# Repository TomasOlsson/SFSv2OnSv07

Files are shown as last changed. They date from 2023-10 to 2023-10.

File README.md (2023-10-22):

# SFSv2OnSv07
How to add BTT SFS V2.0 on Sovol Sv07 and Sv07 Plus

Join our discord server Just another 3D printer community: https://discord.gg/SBAAEH9qnD

# What you need
1. SFS V2.0
2. Printed part of couplerholderV0.3.3mf and SFSV2Holder.3mf
3. Tools

**IF YOU HAVE AN SV07 PLUS, YOU WILL NEED TO EXTEND THE CABLE THAT COMES WITH THE SFS V2.0 OR BUY A LONGER ONE.**

# How to
1. Remove the button plate of the printer.
2. Unconnect the old filament Runout sensor and remove it.
3. Connect the SFS V2.0.

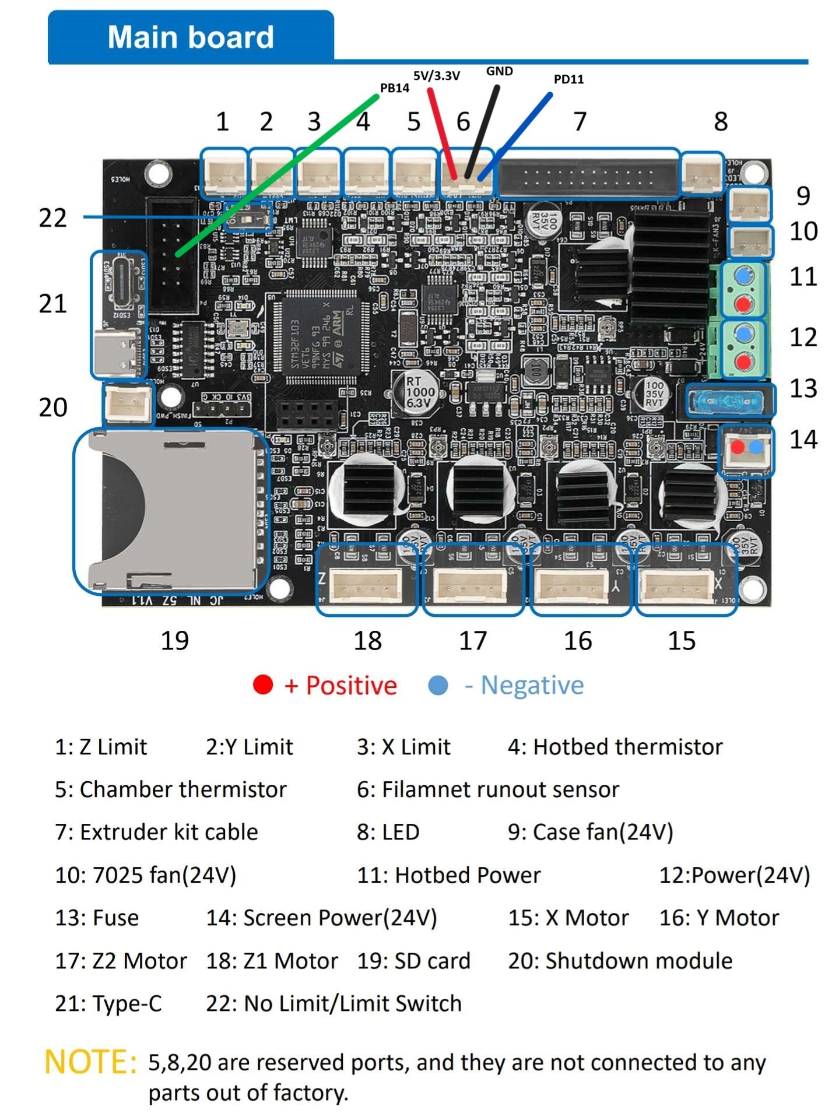
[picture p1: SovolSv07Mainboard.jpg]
Mainboard


4. Run the SFS V2.0 wire where the old runout sensor wire is.
5. Mount the printed parts and the SFS V2.0
6. Add the button plate of the printer.
7. Start printer.
8. Edit printer.cfg

   Remove:
   ```
    [filament_switch_sensor my_sensor]
    #pause_on_runout: True
    #runout_gcode:
    #RESPOND TYPE=error MSG="Filament Runout! Please change filament!"
    #event_delay: 3.0
    #pause_delay: 0.5
    switch_pin:PD11
   ```

   Add:

   ```
   [filament_switch_sensor switch_sensor]
   switch_pin: PD11
   pause_on_runout: False
   runout_gcode:
     PAUSE #[pause_resume] is required in printer.cfg
     RESPOND TYPE=error MSG="No filament was detected!"
   insert_gcode:
     RESPOND TYPE=echo MSG="Filament was inserted"

   [filament_motion_sensor encoder_sensor]
   switch_pin: ^PB14
   detection_length: 3
   extruder: extruder
   pause_on_runout: False
   runout_gcode:
     PAUSE # [pause_resume] is required in printer.cfg
     RESPOND TYPE=error MSG="Filament is stuck!"
   insert_gcode:
     RESPOND TYPE=echo MSG="Filament was inserted"
   ```
9. Save and restart.
10. Check if its working:

    Mainsail: Under dashboard you will see:

    Mainsail

    Fluidd: You will find it under the page "Tune"

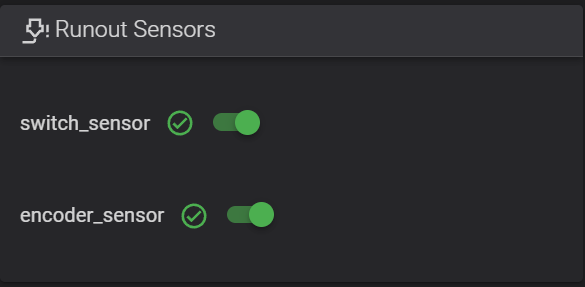
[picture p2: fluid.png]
Fluidd
    

12. If everything checks out try to print.

    # HAPPY PRINTING

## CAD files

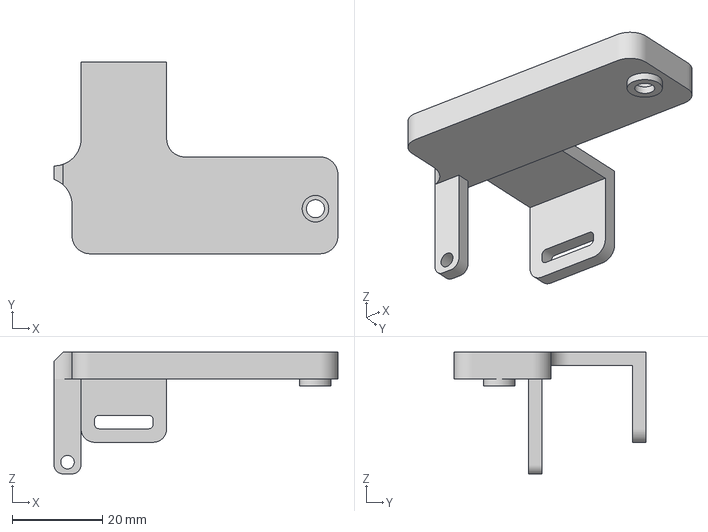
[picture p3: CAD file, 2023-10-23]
couplerholderV0.4.3mf
63.0 x 42.5 x 27.0 mm

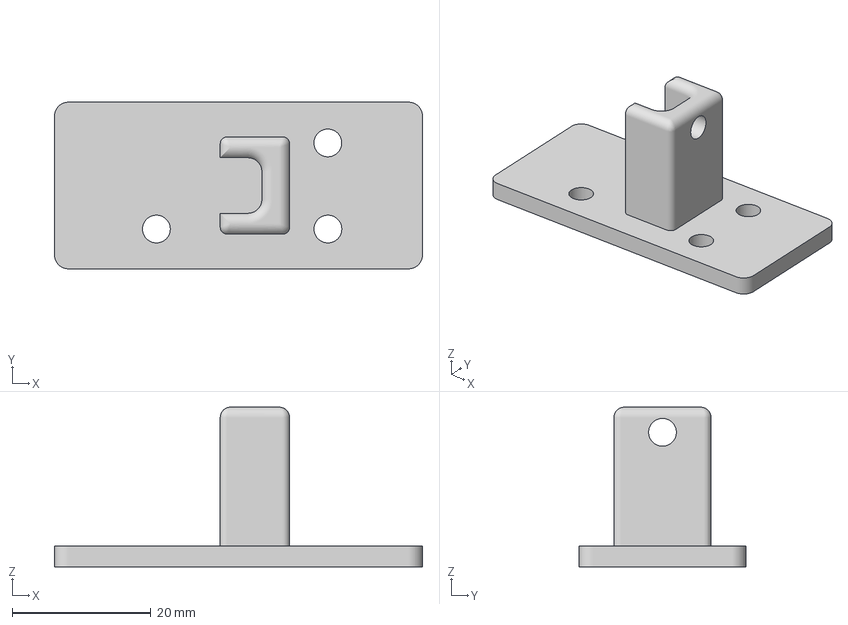
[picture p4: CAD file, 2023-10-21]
SFSV2Holder.3mf
53.0 x 24.0 x 23.0 mm

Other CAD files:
couplerholderV0.3.3mf

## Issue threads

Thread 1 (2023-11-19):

default resume print macro refers to my_sensor.

vasyl83, 2023-11-19:
You need to update your guide to modify the default RESUME macro in printer.cfg to not refer to my_sensor. You need to replace the reference to it with switch_sensor, if not you won't be able to resume printing.

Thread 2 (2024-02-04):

Will this wiring also work on SV06?

TommyStrobbe, 2024-02-04:
I wonder if this wiring also will work on sv06 since the motherboard doesn't look too different ?

GTreaper, 2024-02-04:
> I wonder if this wiring also will work on sv06 since the motherboard doesn't look too different ?

Hello!
Co maker of this project here
Yes wiring should work on sv06 but I'm not sure the pins are named the same on the sv06 as the sv07. Since sv06 is open source, finding the pinouts for the 06 should be alot easier.
Im omw to bed now as I have work tomorrow but if you can't find any pin name yourself I will do my best to find pin names for sv06 if they differ tomorrow after work.

I myself have a 06plus but currently can't check it as its printing parts for another 20-25 hours.

I'll set a reminder for tomorrow afternoon and will do some research for you.

Best regards GTreaper

TommyStrobbe, 2024-02-05:
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

Hi,

Thanks for the reply, i'm a bit wiser now, I use the sfs with the motion side only so I only have 3 wire connector in the 'runout sensor slot' (PA4) on the sv06 atm, after i connected this it worked properly ( only motion function ) but after some testing (2hours later ) the printer started dooing weird ( bad movement, bad exetrute, reading wrong temperatures from
Bed and heatblock...) motherboard started smoking 🤦‍♂️, i measured the out (PA4) and it pulses 3,3V when running filament trough.. Sovol is sending me a new motherboard, but I NEED to know why this happened, I programmed this in klipper as ( switch_pin: !PA4 ) but maybe I need to add '^' in front of it ? Maybe it's coincidence and the motherboard overheated ?

I didn't find a pinout plan for the sv06 but I did for the ender 3 and I guess it's more or less the same( attachement), and the wire on the connector u used on the display port for the switch contact is already used for my lcd screen so no option, i do have free connectors from x y z endstops, so i was thinking maybe i could use one of these (Maybe PA7) 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

TomasOlsson, 2024-02-05:
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

Hello, i read somewhere not to push 3.3v or 5v via the encoder. It can kill the MCU. If you dont have the "orginal" screen you can use pin PB12 or PB13 for the encoder and PA4 for the switch.

TommyStrobbe, 2024-02-05:
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

Hi, thanks for the reply, this could explain the defect!, the pulses are too much to handle for the 3,3v then i guess ? I know some people use these PA4 slot for the older sfs with encoder tho , I might buy a touch screen so the PB 12 comes free.

TomasOlsson, 2024-02-05:
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

Can you send me a link for the pinouts for the card? I can see if there is any fitted pin for you :)

TommyStrobbe, 2024-02-05:
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

Shure, i didn't find inexpensive for sv06 but the ender 3 is almost identical i think : https://github.com/Creality3DPrinting/Ender-3/files/7626788/1623133432-Creality422-Schematic-2.pdf
Thanks !

TommyStrobbe, 2024-03-01:
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

Hi, did u find a fitted pin ?,

I received a new motherboard and am a bit scared to smoke this one also, do you think i could use the pb14 pin without issues for this motion sensor ? I might remove my lcd screen for this
